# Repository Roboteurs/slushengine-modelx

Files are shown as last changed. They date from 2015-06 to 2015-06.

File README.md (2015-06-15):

# SlushEngine Model:X #

This repository contains the hardware design files for the SlusheEngine. The current design is created on Kicad (BZR 5744). If you wish to contribute to the SlusheEngine project please contact Reiner at info at roboteurs dot com.

If you want to get going on your own project using the SlushEngine please fork it and have fun!

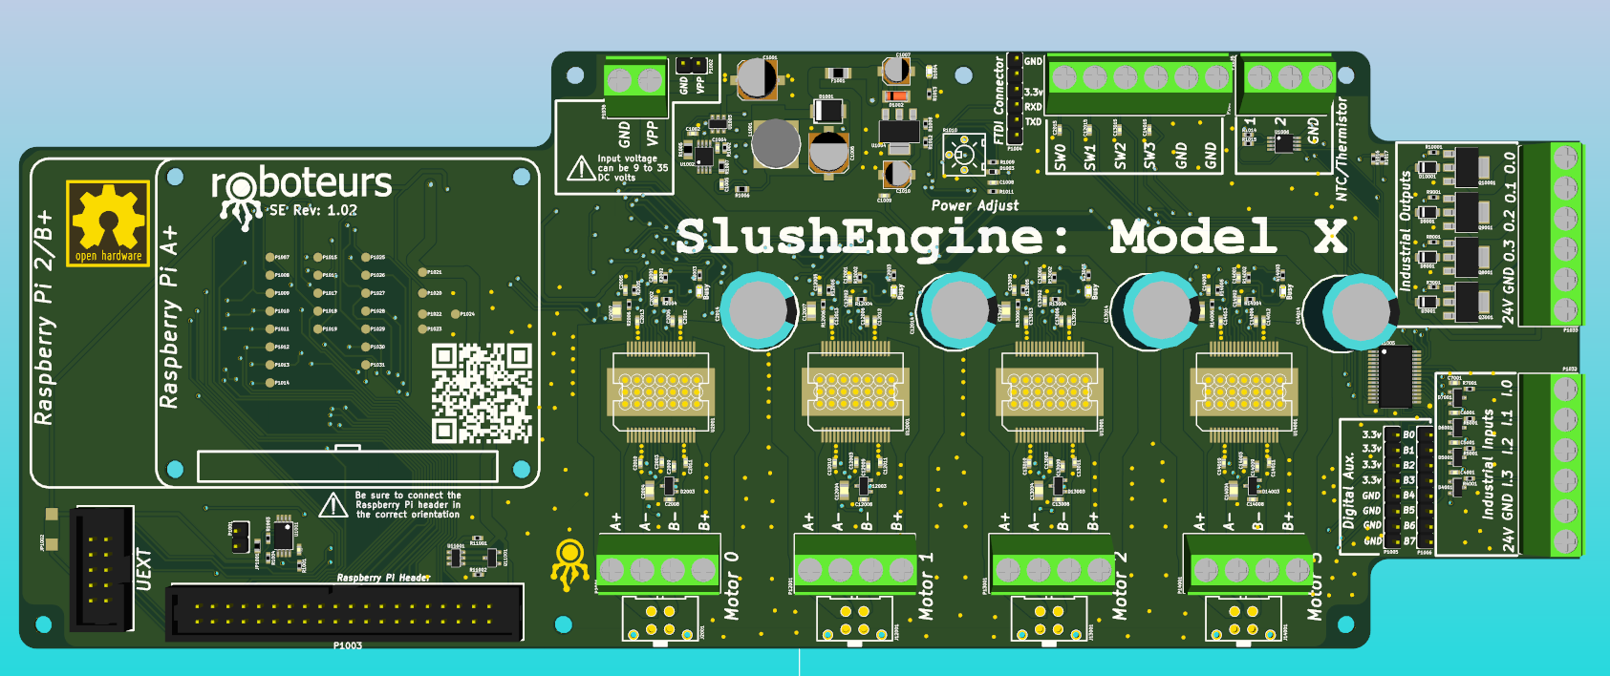
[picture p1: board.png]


## Technical Specifications ##
- Based of L6470 Stepper motor drivers
- Board design to handle 32A on the VPP input
- Supply 5v @ 2A to the Raspberry Pi
- UEXT Connector for expansion modules
- Temperature sensing inputs
- Logic level I/Os and Industrial Level IO (24VDC)
- MAX1164 for temperature sensor handling (2 Channels)
- MCP23017 for I/O expansion on I2C bus
- Raspberry Pi Hat spec eeprom circuit

## Basic Electrical Characteristics ##

- **Max VPP Voltage:** 35VDC
- **Max Current:** 32A
- **No Load Current:** *unkown*
- **Max SPI bus Frequency:** 5Mhz
- **Max Tempratre at L6470L** *unkown*

## Avalible Hardware mods

- **R1010** Can be changed to compensate for off voltage motor (see L6470 datasheet)
- **JP1002** Can be cut to prevent board from powering an expansion module (bottom of the board)

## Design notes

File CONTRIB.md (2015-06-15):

# Contributors and Reference Projects #

We have had a lot of help making the SlushEngine and we want to give credit to all those that helped. Without all of these people, projects and repositories none of this would have been possible.

## Kickstarter Backers ##

Thanks to off you for helping us meet our first production run minimums. Without you SlushEngine would still just be a messy prototype

**Backers Listed in Order of Contribution**
- Dave LeCompte
- Dan Stoneham
- Graham Dixon
- Jerry
- David A. Katz
- James Gonzalez
- Brian Brunswick
- Chris Egloff
- Martin Pike
- Ricardo
- Clive Rixson
- Marcin Kaminski
- SaltyBrains
- Nikolay Kostov
- Davey Rance
- Brian Roy
- Christopher Schneider
- Steve Sutherland
- Pascal M.
- Antony T Curtis
- Drew Harris
- Blufaminol
- John Joseph Mase
- John Vanderlans
- Aaron Price
- George Hope
- Thean Ping
- Jürgen Wittschen
- Ben Hudson
- Tobias Franke
- David B Murray
- Carole Johnston
- Lou O'Block
- John Meyer
- Patrick Dagert
- InSource.Pro
- Mr. Gabor Draskoczy, quickcoating GmbH
- Stan Logan
- MK
- k1ck*thi5
- Chitra
- Tammy Hwang
- Melanie Sodtka
- Alexandru Stan
- Andrew Rossignol
- Shelley McQuade
- Francisco Valera
- David Toma
- Paul Grossman
- Paolo
- GIN
- Charles Burke
- Douglas Petican
- Joon Kim
- Leland Morrison
- Cassandra Dambrosio
- Rikard Westman
- Alice Yeh
- Kelly McDaniel
- Kristen Dyrr
- Axiom Audio
- Julio Terra
- Bogdan Drema

## Project Contributors ##

There are many components to the Slush system and its not easy developing it. But a good team can really help get the Job done, and these poeple where a part of that team.

Alexandru Stan - http://hypertriangle.com/
Andrew Rossignol - http://www.theresistornetwork.com/

## Refrence Projects and Software Tools ##

One of the cool things about the SlushEngine is that it was developed entirely using open source tools! We want to give credit to those tools so that other people can use them as well. There are many diffrent tools that where used and if we missed one please let us know so we can update the list.

- Kicad  http://www.kicad-pcb.org
- Python  https://www.python.org
- Raspberry Pi Foundation - https://www.raspberrypi.org/
- github https://github.com/
- Quick2Wire https://github.com/quick2wire
- SPIDev https://github.com/doceme/py-spidev
- Olimex (UEXT) https://www.olimex.com/

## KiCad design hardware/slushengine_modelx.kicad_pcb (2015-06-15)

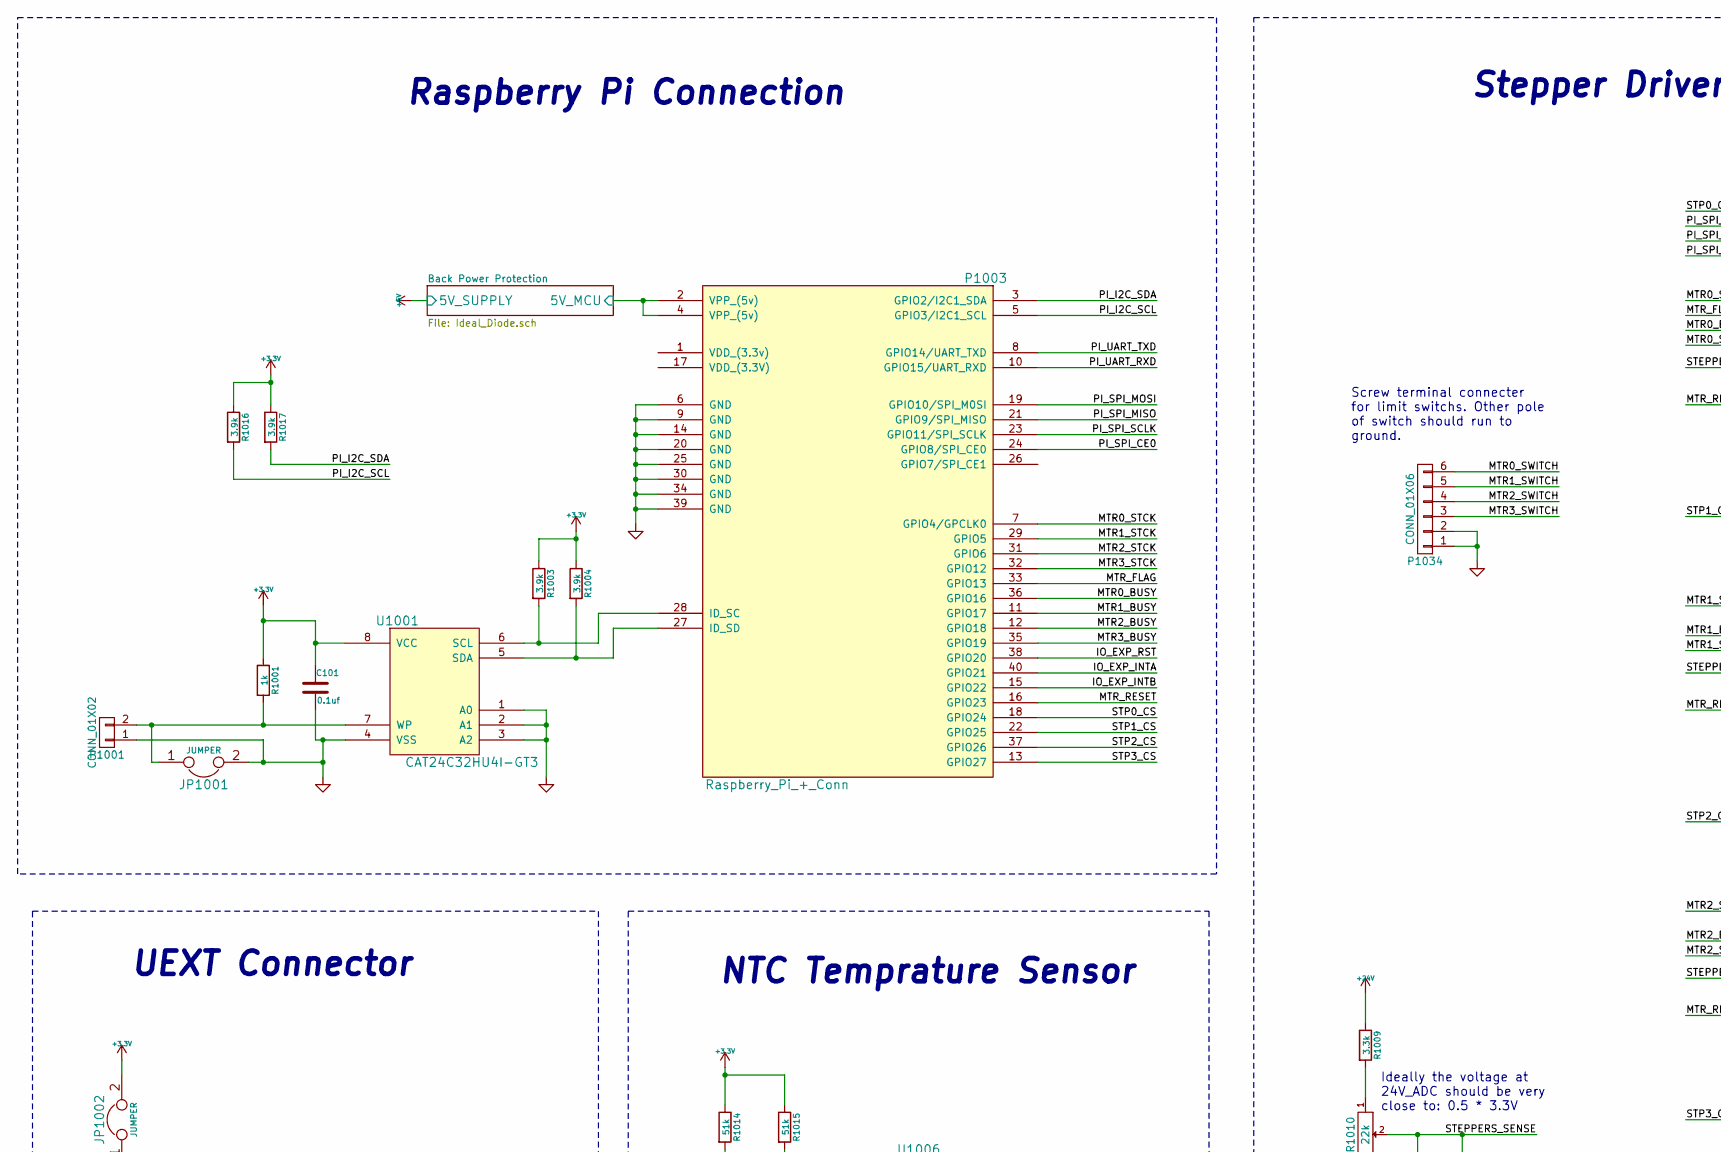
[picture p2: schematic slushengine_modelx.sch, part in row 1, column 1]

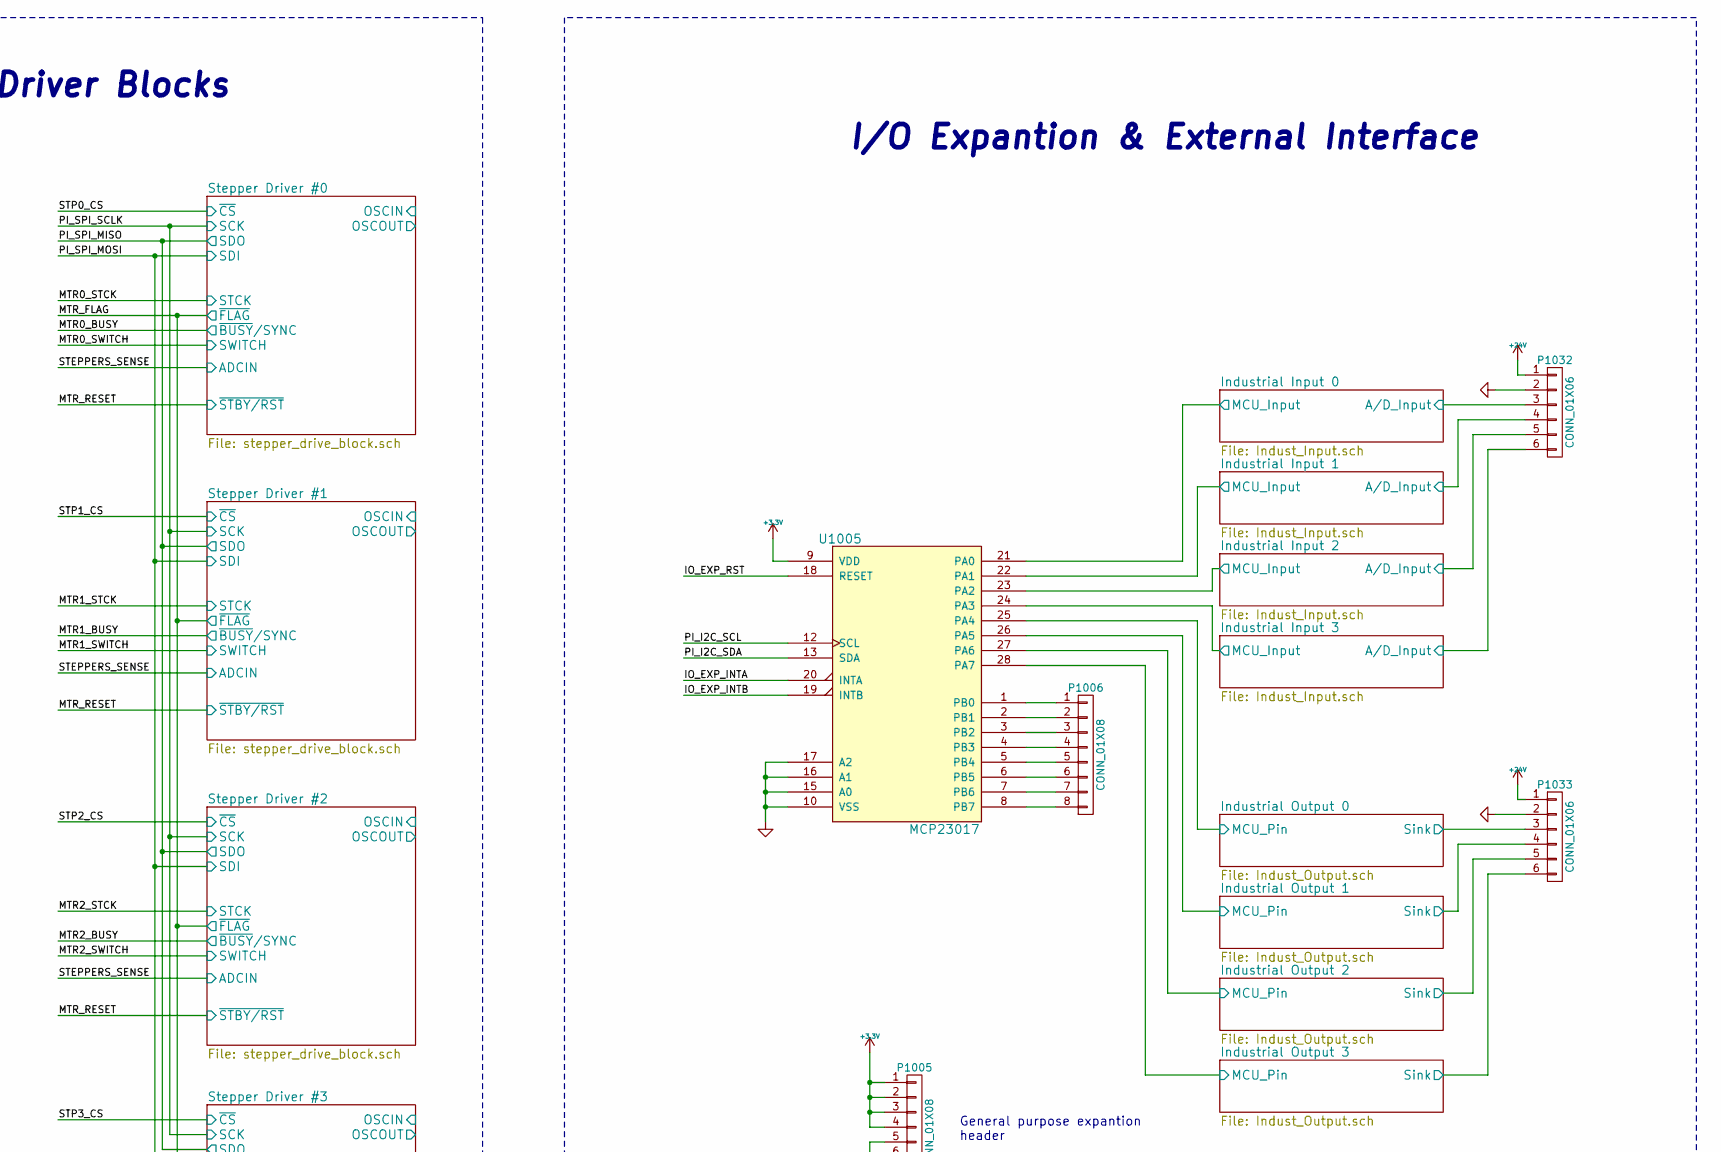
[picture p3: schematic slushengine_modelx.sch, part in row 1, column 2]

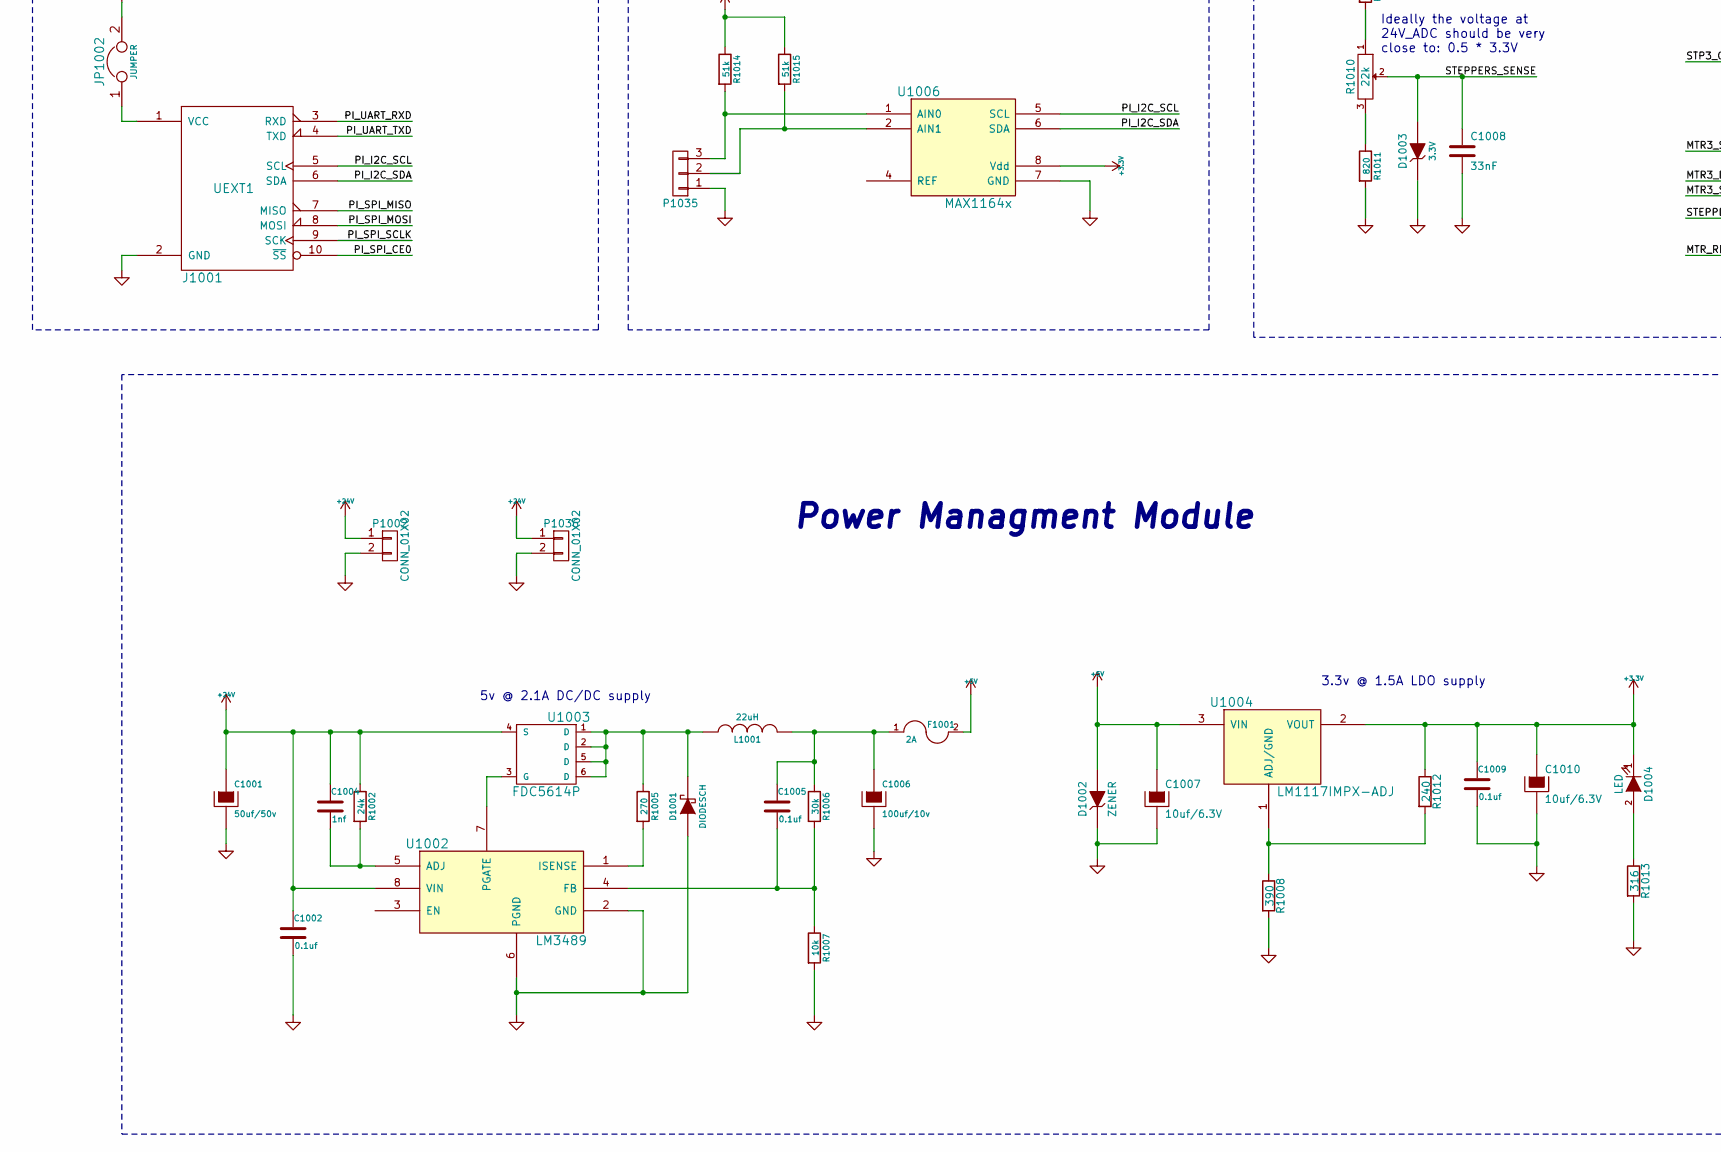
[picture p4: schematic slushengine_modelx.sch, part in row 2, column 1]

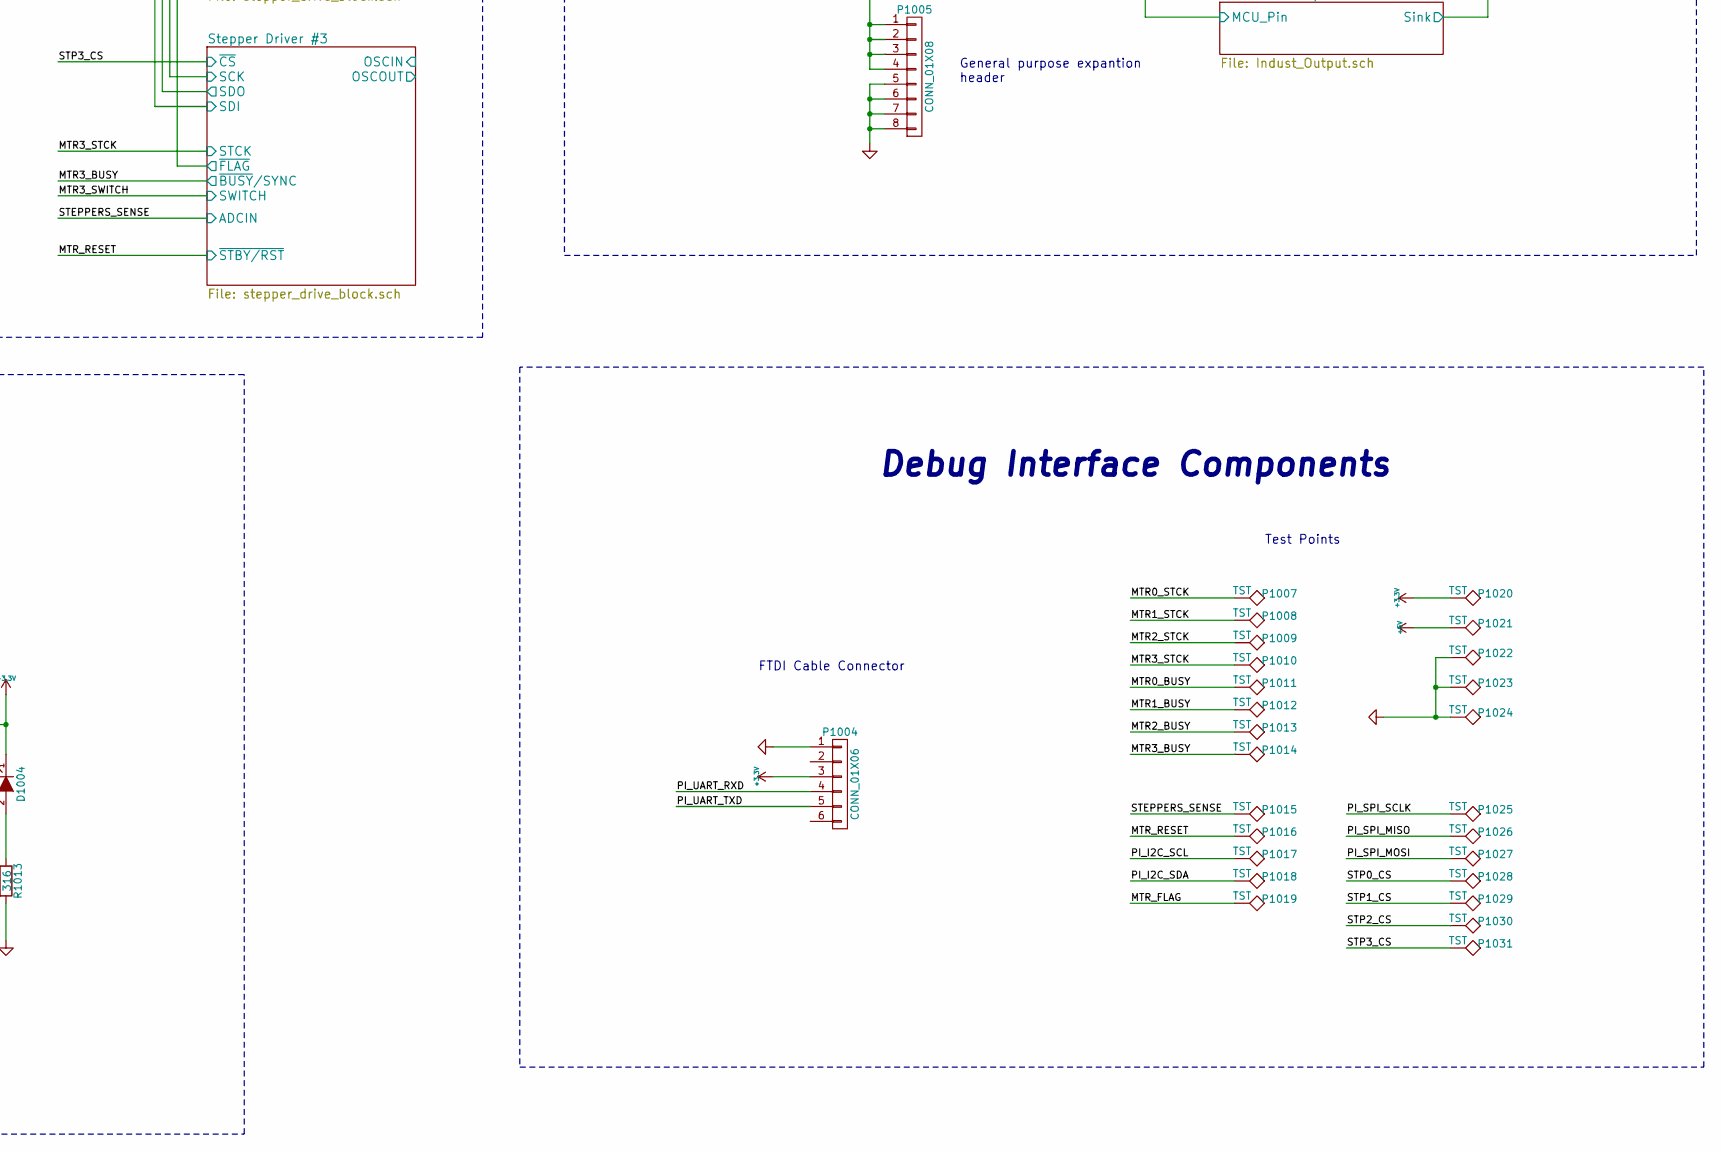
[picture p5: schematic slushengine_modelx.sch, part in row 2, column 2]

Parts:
C101, C1002, C1005, C1009: 0.1uf; c_0402; Mouser Part No. 810-C1005X5R1H104K
C1001: 50uf/50v; c_elec_6.3x7.7; Mouser Part No. 647-UUR1H470MCL6GS
C1004: 1nf; c_0402; Mouser Part No. 810-C1005X5R1H102K
C1006: 100uf/10v; c_elec_6.3x7.7; Mouser Part No. 80-EEV107M016A9GAA
C1007, C1010: 10uf/6.3V; c_elec_4x5.3; Mouser Part No. 80-EEV106M025A9BAA
C1008: 33nF; c_0402; Mouser Part No. 81-GRM36X333K10; Digikey Number 1276-2042-1-ND
D1001: DIODESCH; do214aa; Mouser Part No. 512-MBRS140
D1002: ZENER; sod80c; Mouser Part No. 771-BZV55-C6V2-T/R
D1003: 3.3V; sod523; Mouser Part No. 652-CD0603-Z3V3; Digikey Number CD0603-Z3V3CT-ND
D1004: LED; Led_0603; Mouser Part No. 720-LSQ976-NR-1
F1001: 2A; r_1206; Mouser Part No. 652-MF-NSMF200-2
J1001: UEXT1; vasch_strip_5x2; Mouser Part No. 517-30310-6002; Digikey Number ED1543-ND
JP1001: JUMPER; r_0603
JP1002: JUMPER; NetTie-I_Connected_SMD
L1001: 22uH; inductor_smd_8x5mm; Mouser Part No. 652-SRN8040-220M
P1001: CONN_01X02; pin_strip_2
P1002: CONN_01X02; pin_strip_2; Mouser Part No. 651-1715022
P1003: Raspberry_Pi_+_Conn; vasch_strip_20x2; Mouser Part No. 517-30340-6002
P1004: CONN_01X06; pin_strip_6
P1005, P1006: CONN_01X08; pin_strip_8
P1007, P1008, P1009, P1010, P1011, P1012, P1013, P1014, P1015, P1016, P1017, P1018, P1019, P1020, P1021, P1022, P1023, P1024, P1025, P1026, P1027, P1028, P1029, P1030, P1031: TST; Measurement_Point_Round-SMD-Pad_Small
P1032, P1033, P1034: CONN_01X06; mkds_1,5-6; Mouser Part No. 651-1729160
P1035: CONN_01X03; mkds_1,5-3
P1036: CONN_01X02; mkds_1,5-2
R1001: 1k; r_0402; Mouser Part No. 754-RR0510P-102D
R1002: 24k; r_0402; Mouser Part No. 71-CRCW0402-24K-E3
R1003, R1004, R1016, R1017: 3.9k; r_0402; Mouser Part No. 71-CRCW04023K90FKED
R1005: 270; r_0805; Mouser Part No. 667-ERJ-P06J271V
R1006: 30k; r_0603; Mouser Part No. 594-MCT06030C3002FP5
R1007: 10k; r_0603; Mouser Part No. 71-CRCW0603-10K-E3
R1008: 390; r_0402; Mouser Part No. 594-MCT06030C3900FP5
R1009: 3.3k; r_0402; Mouser Part No. 71-CRCW0402-3.3K-E3; Digikey Number RHM3.3KBGCT-ND
R1010: 22k; 25PR20KLF; Mouser Part No. 858-25PR20KLF
R1011: 820; r_0402; Mouser Part No. 754-RR0510P-821D; Digikey Number 1276-5060-1-ND
R1012: 240; r_0402; Mouser Part No. 754-RR0816P-241D
R1013: 316; r_0402; Mouser Part No. 667-ERJ-2RKF3160X
R1014, R1015: 51k; r_0402; Mouser Part No. 754-RR0510P-513D; Digikey Number 71-CRCW0402-50K-E3
U1001: CAT24C32HU4I-GT3; tssop-8; Mouser Part No. 698-CAT24C32YI-GT3
U1002: LM3489; msoic-8; Mouser Part No. 926-LM3489MM/NOPB
U1003: FDC5614P; sot23-6; Mouser Part No. 512-FDC5614P
U1004: LM1117IMPX-ADJ; sot223; Mouser Part No. 926-M1117IMPXADJNOPB
U1005: MCP23017; ssop-28; Mouser Part No. 579-MCP23017T-E/SS
U1006: MAX1164x; msoic-8; Mouser Part No. 700-MAX11647EUA

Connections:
+3V3: C101.1, C1009.1, C1010.1, D1004.1 (K), JP1002.2, P1004.3, P1005.1, P1005.2, P1005.3, P1005.4, P1020.1, R1001.1, R1003.1, R1004.1, R1012.1, R1014.1, R1015.1, R1016.1, R1017.1, U1001.8 (VCC), U1004.2 (VOUT), U1005.9 (VDD), U1006.8 (Vdd); also elsewhere on the board
+5V: C1007.1, D1002.2 (A), F1001.2, P1021.1, U1004.3 (VIN); also elsewhere on the board
+24V: C1001.1, C1002.1, C1004.1, P1002.1, P1032.1, P1033.1, P1036.1, R1002.1, R1009.1, U1002.8 (VIN), U1003.4 (S); also elsewhere on the board
/Back Power Protection/5V_MCU: P1003.2 (VPP_(5v)), P1003.4 (VPP_(5v)); also elsewhere on the board
/IO_EXP_INTA: P1003.40 (GPIO21), U1005.20 (INTA)
/IO_EXP_INTB: P1003.15 (GPIO22), U1005.19 (INTB)
/IO_EXP_RST: P1003.38 (GPIO20), U1005.18 (RESET)
/Industrial Input 0/A/D_Input: P1032.3; also elsewhere on the board
/Industrial Input 0/MCU_Input: U1005.21 (PA0); also elsewhere on the board
/Industrial Input 1/A/D_Input: P1032.4; also elsewhere on the board
/Industrial Input 1/MCU_Input: U1005.22 (PA1); also elsewhere on the board
/Industrial Input 2/A/D_Input: P1032.5; also elsewhere on the board
/Industrial Input 2/MCU_Input: U1005.23 (PA2); also elsewhere on the board
/Industrial Input 3/A/D_Input: P1032.6; also elsewhere on the board
/Industrial Input 3/MCU_Input: U1005.24 (PA3); also elsewhere on the board
/Industrial Output 0/MCU_Pin: U1005.25 (PA4); also elsewhere on the board
/Industrial Output 0/Sink: P1033.3; also elsewhere on the board
/Industrial Output 1/MCU_Pin: U1005.26 (PA5); also elsewhere on the board
/Industrial Output 1/Sink: P1033.4; also elsewhere on the board
/Industrial Output 2/MCU_Pin: U1005.27 (PA6); also elsewhere on the board
/Industrial Output 2/Sink: P1033.5; also elsewhere on the board
/Industrial Output 3/MCU_Pin: U1005.28 (PA7); also elsewhere on the board
/Industrial Output 3/Sink: P1033.6; also elsewhere on the board
/PI_I2C_SCL: J1001.5 (SCL), P1003.5 (GPIO3/I2C1_SCL), P1017.1, R1016.2, U1005.12 (SCL), U1006.5 (SCL)
/PI_I2C_SDA: J1001.6 (SDA), P1003.3 (GPIO2/I2C1_SDA), P1018.1, R1017.2, U1005.13 (SDA), U1006.6 (SDA)
/PI_SPI_CE0: J1001.10 (~SS), P1003.24 (GPIO8/SPI_CE0)
/PI_UART_RXD: J1001.3 (RXD), P1003.10 (GPIO15/UART_RXD), P1004.4
/PI_UART_TXD: J1001.4 (TXD), P1003.8 (GPIO14/UART_TXD), P1004.5
/Stepper Driver #0/ADCIN: C1008.1, D1003.2 (A), P1015.1, R1010.2; also elsewhere on the board
/Stepper Driver #0/SCK: J1001.9 (SCK), P1003.23 (GPIO11/SPI_SCLK), P1025.1; also elsewhere on the board
/Stepper Driver #0/SDI: J1001.8 (MOSI), P1003.19 (GPIO10/SPI_M0SI), P1027.1; also elsewhere on the board
/Stepper Driver #0/SDO: J1001.7 (MISO), P1003.21 (GPIO9/SPI_MISO), P1026.1; also elsewhere on the board
/Stepper Driver #0/STCK: P1003.7 (GPIO4/GPCLK0), P1007.1; also elsewhere on the board
/Stepper Driver #0/~BUSY~/SYNC: P1003.36 (GPIO16), P1011.1; also elsewhere on the board
/Stepper Driver #0/~CS: P1003.18 (GPIO24), P1028.1; also elsewhere on the board
/Stepper Driver #0/~FLAG: P1003.33 (GPIO13), P1019.1; also elsewhere on the board
/Stepper Driver #0/~STBY/RST: P1003.16 (GPIO23), P1016.1; also elsewhere on the board
/Stepper Driver #1/STCK: P1003.29 (GPIO5), P1008.1; also elsewhere on the board
/Stepper Driver #1/~BUSY~/SYNC: P1003.11 (GPIO17), P1012.1; also elsewhere on the board
/Stepper Driver #1/~CS: P1003.22 (GPIO25), P1029.1; also elsewhere on the board
/Stepper Driver #2/STCK: P1003.31 (GPIO6), P1009.1; also elsewhere on the board
/Stepper Driver #2/SWITCH: P1034.4; also elsewhere on the board
/Stepper Driver #2/~BUSY~/SYNC: P1003.12 (GPIO18), P1013.1; also elsewhere on the board
/Stepper Driver #2/~CS: P1003.37 (GPIO26), P1030.1; also elsewhere on the board
/Stepper Driver #3/STCK: P1003.32 (GPIO12), P1010.1; also elsewhere on the board
/Stepper Driver #3/SWITCH: P1034.3; also elsewhere on the board
/Stepper Driver #3/~BUSY~/SYNC: P1003.35 (GPIO19), P1014.1; also elsewhere on the board
/Stepper Driver #3/~CS: P1003.13 (GPIO27), P1031.1; also elsewhere on the board
GND: C101.2, C1001.2, C1002.2, C1006.2, C1007.2, C1008.2, C1009.2, C1010.2, D1001.1 (A), D1002.1 (K), D1003.1 (K), J1001.2 (GND), JP1001.2, P1001.1, P1002.2, P1003.6 (GND), P1003.9 (GND), P1003.14 (GND), P1003.20 (GND), P1003.25 (GND), P1003.30 (GND), P1003.34 (GND), P1003.39 (GND), P1004.1, P1005.5, P1005.6, P1005.7, P1005.8, P1022.1, P1023.1, P1024.1, P1032.2, P1033.2, P1034.1, P1034.2, P1035.1, P1036.2, R1007.2, R1008.2, R1011.2, R1013.2, U1001.1 (A0), U1001.2 (A1), U1001.3 (A2), U1001.4 (VSS), U1002.2 (GND), U1002.6 (PGND), U1005.10 (VSS), U1005.15 (A0), U1005.16 (A1), U1005.17 (A2), U1006.7 (GND); also elsewhere on the board
unnamed: C1004.2, R1002.2, U1002.5 (ADJ)
unnamed: C1005.1, C1006.1, F1001.1, L1001.2, R1006.1
unnamed: C1005.2, R1006.2, R1007.1, U1002.4 (FB)
unnamed: D1001.2 (K), L1001.1, R1005.1, U1003.1 (D), U1003.2 (D), U1003.5 (D), U1003.6 (D)
unnamed: D1004.2 (A), R1013.1
unnamed: J1001.1 (VCC), JP1002.1
unnamed: JP1001.1, P1001.2, R1001.2, U1001.7 (WP)
unnamed: P1003.27 (ID_SD), R1004.2, U1001.5 (SDA)
unnamed: P1003.28 (ID_SC), R1003.2, U1001.6 (SCL)
unnamed: P1006.1, U1005.1 (PB0)
unnamed: P1006.2, U1005.2 (PB1)
unnamed: P1006.3, U1005.3 (PB2)
unnamed: P1006.4, U1005.4 (PB3)
unnamed: P1006.5, U1005.5 (PB4)
unnamed: P1006.6, U1005.6 (PB5)
unnamed: P1006.7, U1005.7 (PB6)
unnamed: P1006.8, U1005.8 (PB7)
unnamed: P1035.2, R1015.2, U1006.2 (AIN1)
unnamed: P1035.3, R1014.2, U1006.1 (AIN0)
unnamed: R1005.2, U1002.1 (ISENSE)
unnamed: R1008.1, R1012.2, U1004.1 (ADJ/GND)
unnamed: R1009.2, R1010.1
unnamed: R1010.3, R1011.1
unnamed: U1002.7 (PGATE), U1003.3 (G)

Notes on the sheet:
Ideally the voltage at 24V_ADC should be very close to: 0.5 * 3.3V
Raspberry Pi Connection
Stepper Driver Blocks
I/O Expantion & External Interface
Power Managment Module
General purpose expantion header
5v @ 2.1A DC/DC supply
3.3v @ 1.5A LDO supply
Debug Interface Components
Test Points
FTDI Cable Connector
UEXT Connector
Screw terminal connecter for limit switchs. Other pole of switch should run to ground.
NTC Temprature Sensor

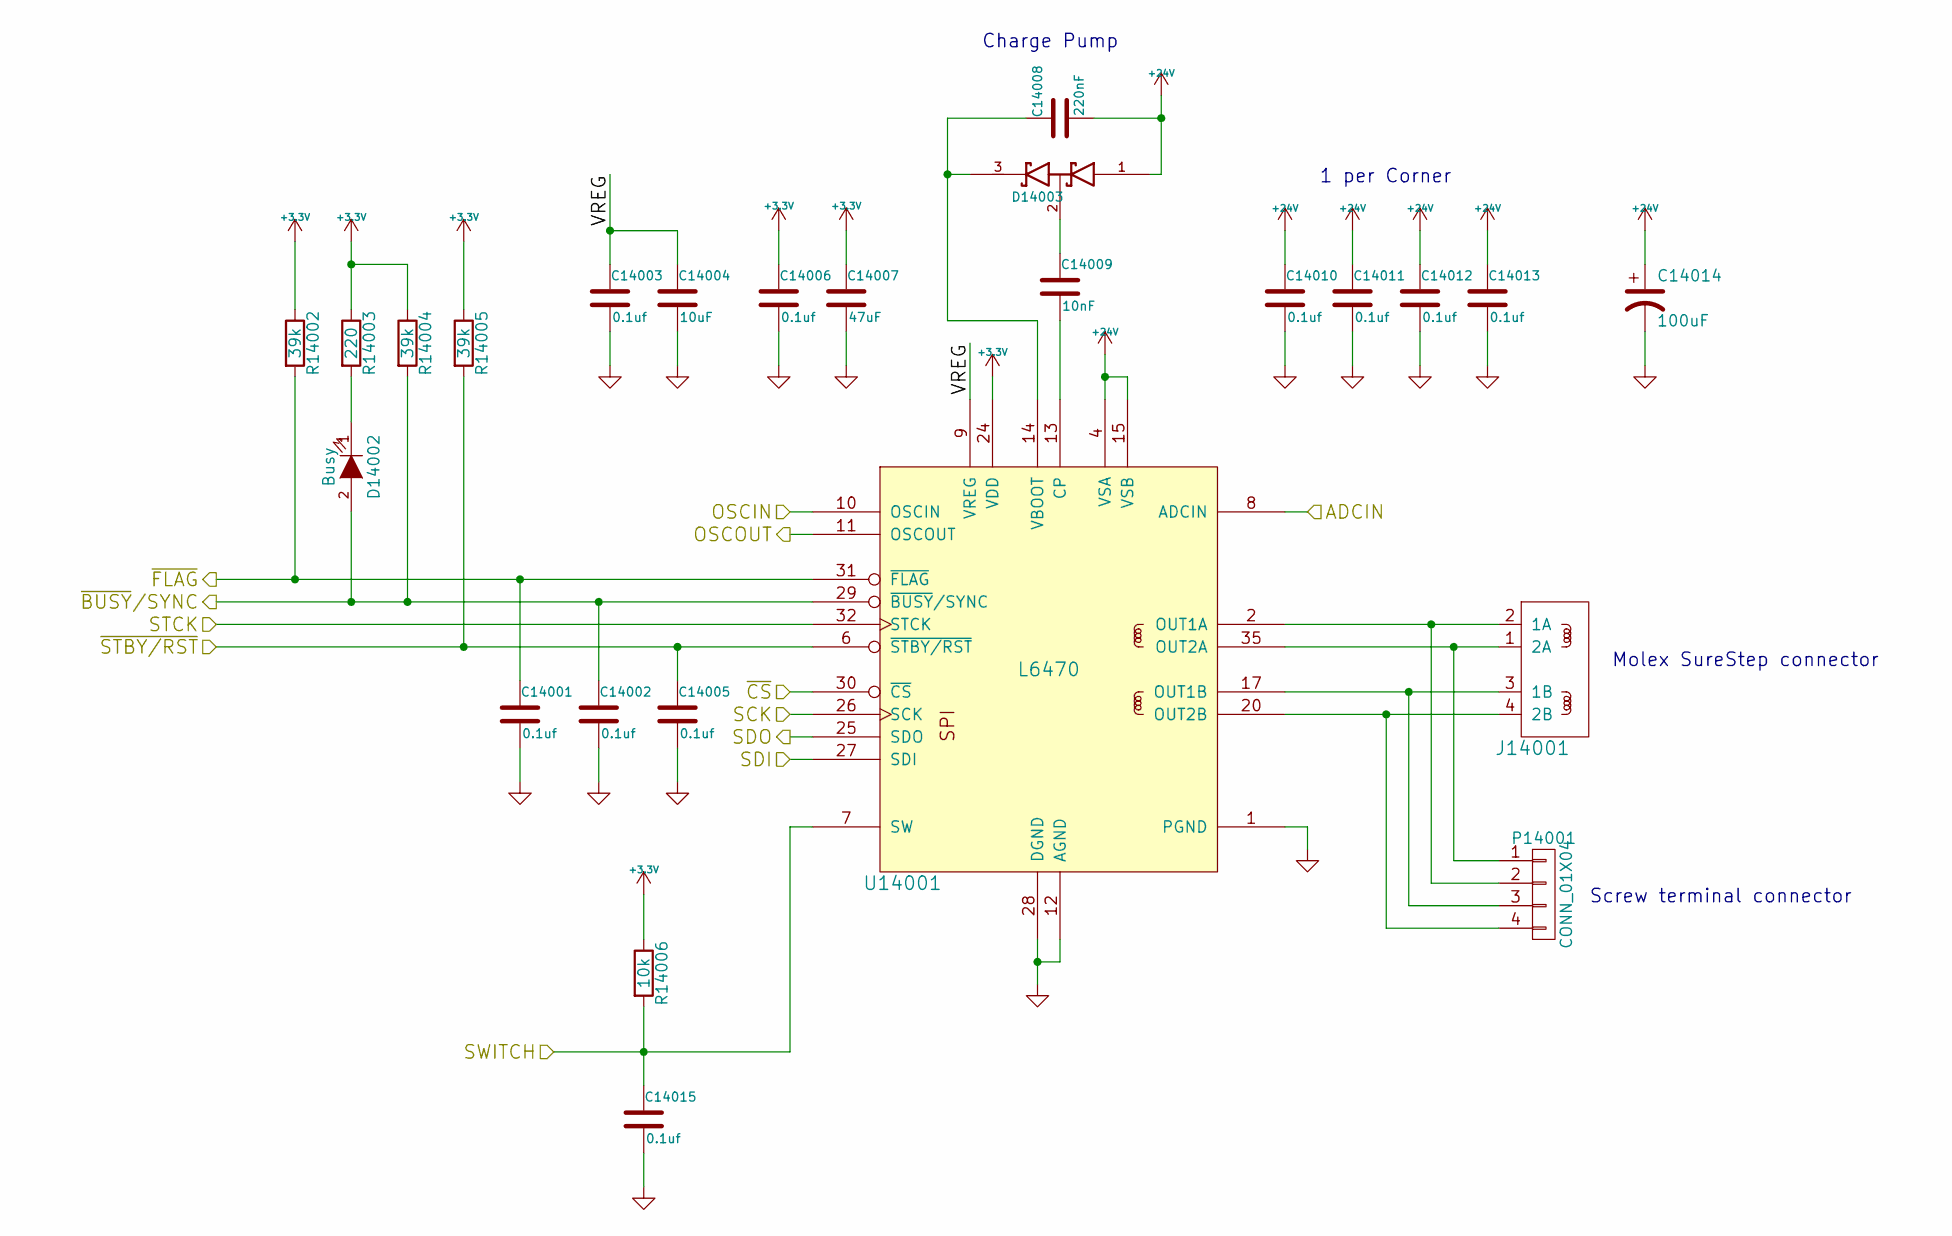
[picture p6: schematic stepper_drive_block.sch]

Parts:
C2001, C2002, C2003, C2005, C2006, C2010, C2011, C2012, C2013, C12015: 0.1uf; c_0402; Mouser Part No. 810-C1005X5R1H104K; Digikey Number 1276-2163-1-ND
C2004: 10uF; c_0805; Mouser Part No. 81-GRM219R61E106KA2D; Digikey Number 1276-1119-1-ND
C2007: 47uF; c_0805; Mouser Part No. 963-JMK212BJ476MG-T; Digikey Number 1276-2420-1-ND
C2008: 220nF; c_0402; Mouser Part No. 810-CGA2B1X7R1V224KC; Digikey Number 1276-2949-1-ND
C2009: 10nF; c_0402; Mouser Part No. 81-GRM155R71H103KA8D; Digikey Number 445-1304-1-ND
C2014: 100uF; CP_12.5x25mm; Mouser Part No. 667-EEU-EE2C101; Digikey Number P13622-ND
D2002: Busy; Led_0603; Mouser Part No. 696-SML-LX0603SUGW; Digikey Number 67-1693-1-ND
D2003: DOUBLE_SCHOTTKY; sot23; Mouser Part No. 833-BAS70-04-TP; Digikey Number BAS70-04TPMSCT-ND
J2001: Stepper Motor; SureStep_CONN; Mouser Part No. 538-43045-0412; Digikey Number 281-1437-ND
P2001: CONN_01X04; mkds_1,5-4; Mouser Part No. 651-1729144
R2002, R2004, R2005: 39k; r_0402; Mouser Part No. 754-RR0510P-393D; Digikey Number 1276-5100-1-ND
R2003: 220; r_0402; Mouser Part No. 667-ERA-2AED221X; Digikey Number 1276-5046-1-ND
R2006: 10k; r_0402; Mouser Part No. 754-RR0510P-103D; Digikey Number 1276-5086-1-ND
U2001: L6470; POWERSO-36; Mouser Part No. 511-L6470PD

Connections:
+3V3: C2006.1, C2007.1, R2002.1, R2003.1, R2004.1, R2005.1, R2006.1, U2001.24 (VDD); also elsewhere on the board
+24V: C2008.2, C2010.1, C2011.1, C2012.1, C2013.1, C2014.1, D2003.1 (Anode), U2001.4 (VSA), U2001.5 (VSA), U2001.15 (VSB), U2001.16 (VSB), U2001.22 (VSB), U2001.23 (VSB), U2001.33 (VSA), U2001.34 (VSA); also elsewhere on the board
/Stepper Driver #0/ADCIN: U2001.8 (ADCIN); also elsewhere on the board
/Stepper Driver #0/OSCIN: U2001.10 (OSCIN)
/Stepper Driver #0/OSCOUT: U2001.11 (OSCOUT)
/Stepper Driver #0/SCK: U2001.26 (SCK); also elsewhere on the board
/Stepper Driver #0/SDI: U2001.27 (SDI); also elsewhere on the board
/Stepper Driver #0/SDO: U2001.25 (SDO); also elsewhere on the board
/Stepper Driver #0/STCK: U2001.32 (STCK); also elsewhere on the board
/Stepper Driver #0/VREG: C2003.1, C2004.1, U2001.9 (VREG)
/Stepper Driver #0/~BUSY~/SYNC: C2002.1, D2002.2 (A), R2004.2, U2001.29 (~BUSY~/SYNC); also elsewhere on the board
/Stepper Driver #0/~CS: U2001.30 (~CS); also elsewhere on the board
/Stepper Driver #0/~FLAG: C2001.1, R2002.2, U2001.31 (~FLAG); also elsewhere on the board
/Stepper Driver #0/~STBY/RST: C2005.1, R2005.2, U2001.6 (~STBY/RST); also elsewhere on the board
GND: C2001.2, C2002.2, C2003.2, C2004.2, C2005.2, C2006.2, C2007.2, C2010.2, C2011.2, C2012.2, C2013.2, C2014.2, C12015.2, U2001.1 (PGND), U2001.12 (AGND), U2001.19 (PGND), U2001.28 (DGND), U2001.PAD (PGND); also elsewhere on the board
unnamed: C2008.1, D2003.3 (cathode), U2001.14 (VBOOT)
unnamed: C2009.1, D2003.2 (AK)
unnamed: C2009.2, U2001.13 (CP)
unnamed: D2002.1 (K), R2003.2
unnamed: J2001.1 (2A), P2001.1, U2001.35 (OUT2A), U2001.36 (OUT2A)
unnamed: J2001.2 (1A), P2001.2, U2001.2 (OUT1A), U2001.3 (OUT1A)
unnamed: J2001.3 (1B), P2001.3, U2001.17 (OUT1B), U2001.18 (OUT1B)
unnamed: J2001.4 (2B), P2001.4, U2001.20 (OUT2B), U2001.21 (OUT2B)

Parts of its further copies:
C2015, C12001, C12002, C12003, C12005, C12006, C12010, C12011, C12012, C12013, C13001, C13002, C13003, C13005, C13006, C13010, C13011, C13012, C13013, C13015, C14001, C14002, C14003, C14005, C14006, C14010, C14011, C14012, C14013, C14015: 0.1uf; c_0402; Mouser Part No. 810-C1005X5R1H104K; Digikey Number 1276-2163-1-ND
C12004, C13004, C14004: 10uF; c_0805; Mouser Part No. 81-GRM219R61E106KA2D; Digikey Number 1276-1119-1-ND
C12007, C13007, C14007: 47uF; c_0805; Mouser Part No. 963-JMK212BJ476MG-T; Digikey Number 1276-2420-1-ND
C12008, C13008, C14008: 220nF; c_0402; Mouser Part No. 810-CGA2B1X7R1V224KC; Digikey Number 1276-2949-1-ND
C12009, C13009, C14009: 10nF; c_0402; Mouser Part No. 81-GRM155R71H103KA8D; Digikey Number 445-1304-1-ND
C12014, C13014, C14014: 100uF; CP_12.5x25mm; Mouser Part No. 667-EEU-EE2C101; Digikey Number P13622-ND
D12002, D13002, D14002: Busy; Led_0603; Mouser Part No. 696-SML-LX0603SUGW; Digikey Number 67-1693-1-ND
D12003, D13003, D14003: DOUBLE_SCHOTTKY; sot23; Mouser Part No. 833-BAS70-04-TP; Digikey Number BAS70-04TPMSCT-ND
J12001, J13001, J14001: Stepper Motor; SureStep_CONN; Mouser Part No. 538-43045-0412; Digikey Number 281-1437-ND
P12001, P13001, P14001: CONN_01X04; mkds_1,5-4; Mouser Part No. 651-1729144
R12002, R12004, R12005, R13002, R13004, R13005, R14002, R14004, R14005: 39k; r_0402; Mouser Part No. 754-RR0510P-393D; Digikey Number 1276-5100-1-ND
R12003, R13003, R14003: 220; r_0402; Mouser Part No. 667-ERA-2AED221X; Digikey Number 1276-5046-1-ND
R12006, R13006, R14006: 10k; r_0402; Mouser Part No. 754-RR0510P-103D; Digikey Number 1276-5086-1-ND
U12001, U13001, U14001: L6470; POWERSO-36; Mouser Part No. 511-L6470PD

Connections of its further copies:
+3V3: C12006.1, C12007.1, C13006.1, C13007.1, C14006.1, C14007.1, R12002.1, R12003.1, R12004.1, R12005.1, R12006.1, R13002.1, R13003.1, R13004.1, R13005.1, R13006.1, R14002.1, R14003.1, R14004.1, R14005.1, R14006.1, U12001.24 (VDD), U13001.24 (VDD), U14001.24 (VDD); also elsewhere on the board
+24V: C12008.2, C12010.1, C12011.1, C12012.1, C12013.1, C12014.1, C13008.2, C13010.1, C13011.1, C13012.1, C13013.1, C13014.1, C14008.2, C14010.1, C14011.1, C14012.1, C14013.1, C14014.1, D12003.1 (Anode), D13003.1 (Anode), D14003.1 (Anode), U12001.4 (VSA), U12001.5 (VSA), U12001.15 (VSB), U12001.16 (VSB), U12001.22 (VSB), U12001.23 (VSB), U12001.33 (VSA), U12001.34 (VSA), U13001.4 (VSA), U13001.5 (VSA), U13001.15 (VSB), U13001.16 (VSB), U13001.22 (VSB), U13001.23 (VSB), U13001.33 (VSA), U13001.34 (VSA), U14001.4 (VSA), U14001.5 (VSA), U14001.15 (VSB), U14001.16 (VSB), U14001.22 (VSB), U14001.23 (VSB), U14001.33 (VSA), U14001.34 (VSA); also elsewhere on the board
/Stepper Driver #0/ADCIN: U12001.8 (ADCIN), U13001.8 (ADCIN), U14001.8 (ADCIN); also elsewhere on the board
/Stepper Driver #0/SCK: U12001.26 (SCK), U13001.26 (SCK), U14001.26 (SCK); also elsewhere on the board
/Stepper Driver #0/SDI: U12001.27 (SDI), U13001.27 (SDI), U14001.27 (SDI); also elsewhere on the board
/Stepper Driver #0/SDO: U12001.25 (SDO), U13001.25 (SDO), U14001.25 (SDO); also elsewhere on the board
/Stepper Driver #0/~FLAG: C12001.1, C13001.1, C14001.1, R12002.2, R13002.2, R14002.2, U12001.31 (~FLAG), U13001.31 (~FLAG), U14001.31 (~FLAG); also elsewhere on the board
/Stepper Driver #0/~STBY/RST: C12005.1, C13005.1, C14005.1, R12005.2, R13005.2, R14005.2, U12001.6 (~STBY/RST), U13001.6 (~STBY/RST), U14001.6 (~STBY/RST); also elsewhere on the board
/Stepper Driver #1/OSCIN: U12001.10 (OSCIN)
/Stepper Driver #1/OSCOUT: U12001.11 (OSCOUT)
/Stepper Driver #1/STCK: U12001.32 (STCK); also elsewhere on the board
/Stepper Driver #1/VREG: C12003.1, C12004.1, U12001.9 (VREG)
/Stepper Driver #1/~BUSY~/SYNC: C12002.1, D12002.2 (A), R12004.2, U12001.29 (~BUSY~/SYNC); also elsewhere on the board
/Stepper Driver #1/~CS: U12001.30 (~CS); also elsewhere on the board
/Stepper Driver #2/OSCIN: U13001.10 (OSCIN)
/Stepper Driver #2/OSCOUT: U13001.11 (OSCOUT)
/Stepper Driver #2/STCK: U13001.32 (STCK); also elsewhere on the board
/Stepper Driver #2/SWITCH: C13015.1, R13006.2, U13001.7 (SW); also elsewhere on the board
/Stepper Driver #2/VREG: C13003.1, C13004.1, U13001.9 (VREG)
/Stepper Driver #2/~BUSY~/SYNC: C13002.1, D13002.2 (A), R13004.2, U13001.29 (~BUSY~/SYNC); also elsewhere on the board
/Stepper Driver #2/~CS: U13001.30 (~CS); also elsewhere on the board
/Stepper Driver #3/OSCIN: U14001.10 (OSCIN)
/Stepper Driver #3/OSCOUT: U14001.11 (OSCOUT)
/Stepper Driver #3/STCK: U14001.32 (STCK); also elsewhere on the board
/Stepper Driver #3/SWITCH: C14015.1, R14006.2, U14001.7 (SW); also elsewhere on the board
/Stepper Driver #3/VREG: C14003.1, C14004.1, U14001.9 (VREG)
/Stepper Driver #3/~BUSY~/SYNC: C14002.1, D14002.2 (A), R14004.2, U14001.29 (~BUSY~/SYNC); also elsewhere on the board
/Stepper Driver #3/~CS: U14001.30 (~CS); also elsewhere on the board
GND: C2015.2, C12001.2, C12002.2, C12003.2, C12004.2, C12005.2, C12006.2, C12007.2, C12010.2, C12011.2, C12012.2, C12013.2, C12014.2, C13001.2, C13002.2, C13003.2, C13004.2, C13005.2, C13006.2, C13007.2, C13010.2, C13011.2, C13012.2, C13013.2, C13014.2, C13015.2, C14001.2, C14002.2, C14003.2, C14004.2, C14005.2, C14006.2, C14007.2, C14010.2, C14011.2, C14012.2, C14013.2, C14014.2, C14015.2, U12001.1 (PGND), U12001.12 (AGND), U12001.19 (PGND), U12001.28 (DGND), U12001.PAD (PGND), U13001.1 (PGND), U13001.12 (AGND), U13001.19 (PGND), U13001.28 (DGND), U13001.PAD (PGND), U14001.1 (PGND), U14001.12 (AGND), U14001.19 (PGND), U14001.28 (DGND), U14001.PAD (PGND); also elsewhere on the board
unnamed: C12008.1, D12003.3 (cathode), U12001.14 (VBOOT)
unnamed: C12009.1, D12003.2 (AK)
unnamed: C12009.2, U12001.13 (CP)
unnamed: C13008.1, D13003.3 (cathode), U13001.14 (VBOOT)
unnamed: C13009.1, D13003.2 (AK)
unnamed: C13009.2, U13001.13 (CP)
unnamed: C14008.1, D14003.3 (cathode), U14001.14 (VBOOT)
unnamed: C14009.1, D14003.2 (AK)
unnamed: C14009.2, U14001.13 (CP)
unnamed: D12002.1 (K), R12003.2
unnamed: D13002.1 (K), R13003.2
unnamed: D14002.1 (K), R14003.2
unnamed: J12001.1 (2A), P12001.1, U12001.35 (OUT2A), U12001.36 (OUT2A)
unnamed: J12001.2 (1A), P12001.2, U12001.2 (OUT1A), U12001.3 (OUT1A)
unnamed: J12001.3 (1B), P12001.3, U12001.17 (OUT1B), U12001.18 (OUT1B)
unnamed: J12001.4 (2B), P12001.4, U12001.20 (OUT2B), U12001.21 (OUT2B)
unnamed: J13001.1 (2A), P13001.1, U13001.35 (OUT2A), U13001.36 (OUT2A)
unnamed: J13001.2 (1A), P13001.2, U13001.2 (OUT1A), U13001.3 (OUT1A)
unnamed: J13001.3 (1B), P13001.3, U13001.17 (OUT1B), U13001.18 (OUT1B)
unnamed: J13001.4 (2B), P13001.4, U13001.20 (OUT2B), U13001.21 (OUT2B)
unnamed: J14001.1 (2A), P14001.1, U14001.35 (OUT2A), U14001.36 (OUT2A)
unnamed: J14001.2 (1A), P14001.2, U14001.2 (OUT1A), U14001.3 (OUT1A)
unnamed: J14001.3 (1B), P14001.3, U14001.17 (OUT1B), U14001.18 (OUT1B)
unnamed: J14001.4 (2B), P14001.4, U14001.20 (OUT2B), U14001.21 (OUT2B)

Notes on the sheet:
1 per Corner
Charge Pump
Molex SureStep connector
Screw terminal connector

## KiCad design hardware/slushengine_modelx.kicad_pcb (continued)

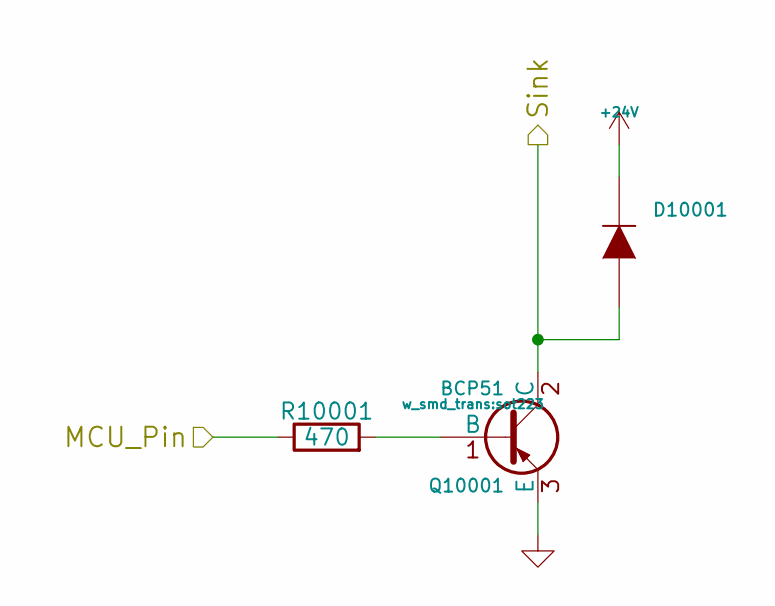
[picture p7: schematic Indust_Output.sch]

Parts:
D3001: RSX501L-20TE25; do219ab; Mouser Part No. 78-S07J; Digikey Number RSX501L-20TE25CT-ND
Q3001: BCP51; sot223; Mouser Part No. 863-NJT4031NT1G
R3001: 470; r_0402; Mouser Part No. 71-CRCW0402-470-E3; Digikey Number 1276-5054-1-ND

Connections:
+24V: D3001.2 (K); also elsewhere on the board
/Industrial Output 0/MCU_Pin: R3001.1; also elsewhere on the board
/Industrial Output 0/Sink: D3001.1 (A), Q3001.2 (C); also elsewhere on the board
GND: Q3001.3 (E); also elsewhere on the board
unnamed: Q3001.1 (B), R3001.2

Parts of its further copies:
D8001, D9001, D10001: RSX501L-20TE25; do219ab; Mouser Part No. 78-S07J; Digikey Number RSX501L-20TE25CT-ND
Q8001, Q9001, Q10001: BCP51; sot223; Mouser Part No. 863-NJT4031NT1G
R8001, R9001, R10001: 470; r_0402; Mouser Part No. 71-CRCW0402-470-E3; Digikey Number 1276-5054-1-ND

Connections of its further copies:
+24V: D8001.2 (K), D9001.2 (K), D10001.2 (K); also elsewhere on the board
/Industrial Output 1/MCU_Pin: R8001.1; also elsewhere on the board
/Industrial Output 1/Sink: D8001.1 (A), Q8001.2 (C); also elsewhere on the board
/Industrial Output 2/MCU_Pin: R9001.1; also elsewhere on the board
/Industrial Output 2/Sink: D9001.1 (A), Q9001.2 (C); also elsewhere on the board
/Industrial Output 3/MCU_Pin: R10001.1; also elsewhere on the board
/Industrial Output 3/Sink: D10001.1 (A), Q10001.2 (C); also elsewhere on the board
GND: Q8001.3 (E), Q9001.3 (E), Q10001.3 (E); also elsewhere on the board
unnamed: Q8001.1 (B), R8001.2
unnamed: Q9001.1 (B), R9001.2
unnamed: Q10001.1 (B), R10001.2

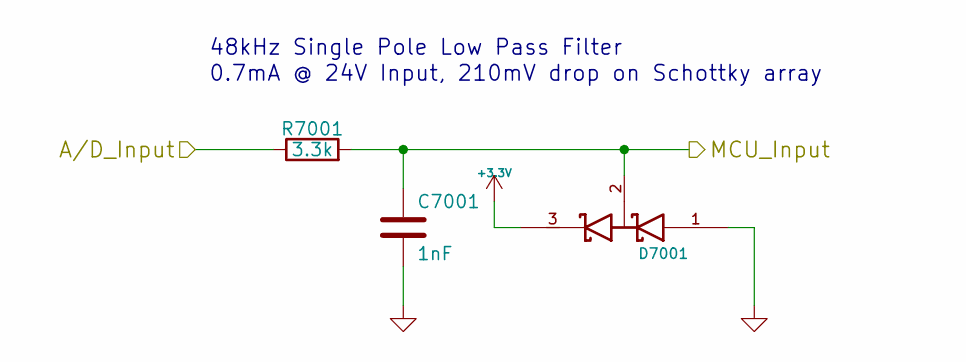
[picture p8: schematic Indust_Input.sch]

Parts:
C4001: 1nF; c_0402; Mouser Part No. 810-C1005C0G2A102J5C; Digikey Number 1276-1913-1-ND
D4001: 1SS295; sot23; Mouser Part No. 757-1SS295TE85LF; Digikey Number 1SS295(TE85LF)CT-ND
R4001: 3.3k; r_0402; Mouser Part No. 71-CRCW0402J-3.3K-E3; Digikey Number RHM3.3KBGCT-ND

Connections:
+3V3: D4001.3 (cathode); also elsewhere on the board
/Industrial Input 0/A/D_Input: R4001.1; also elsewhere on the board
/Industrial Input 0/MCU_Input: C4001.1, D4001.2 (AK), R4001.2; also elsewhere on the board
GND: C4001.2, D4001.1 (Anode); also elsewhere on the board

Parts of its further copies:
C5001, C6001, C7001: 1nF; c_0402; Mouser Part No. 810-C1005C0G2A102J5C; Digikey Number 1276-1913-1-ND
D5001, D6001, D7001: 1SS295; sot23; Mouser Part No. 757-1SS295TE85LF; Digikey Number 1SS295(TE85LF)CT-ND
R5001, R6001, R7001: 3.3k; r_0402; Mouser Part No. 71-CRCW0402J-3.3K-E3; Digikey Number RHM3.3KBGCT-ND

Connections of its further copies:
+3V3: D5001.3 (cathode), D6001.3 (cathode), D7001.3 (cathode); also elsewhere on the board
/Industrial Input 1/A/D_Input: R5001.1; also elsewhere on the board
/Industrial Input 1/MCU_Input: C5001.1, D5001.2 (AK), R5001.2; also elsewhere on the board
/Industrial Input 2/A/D_Input: R6001.1; also elsewhere on the board
/Industrial Input 2/MCU_Input: C6001.1, D6001.2 (AK), R6001.2; also elsewhere on the board
/Industrial Input 3/A/D_Input: R7001.1; also elsewhere on the board
/Industrial Input 3/MCU_Input: C7001.1, D7001.2 (AK), R7001.2; also elsewhere on the board
GND: C5001.2, C6001.2, C7001.2, D5001.1 (Anode), D6001.1 (Anode), D7001.1 (Anode); also elsewhere on the board

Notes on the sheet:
48kHz Single Pole Low Pass Filter
0.7mA @ 24V Input, 210mV drop on Schottky array

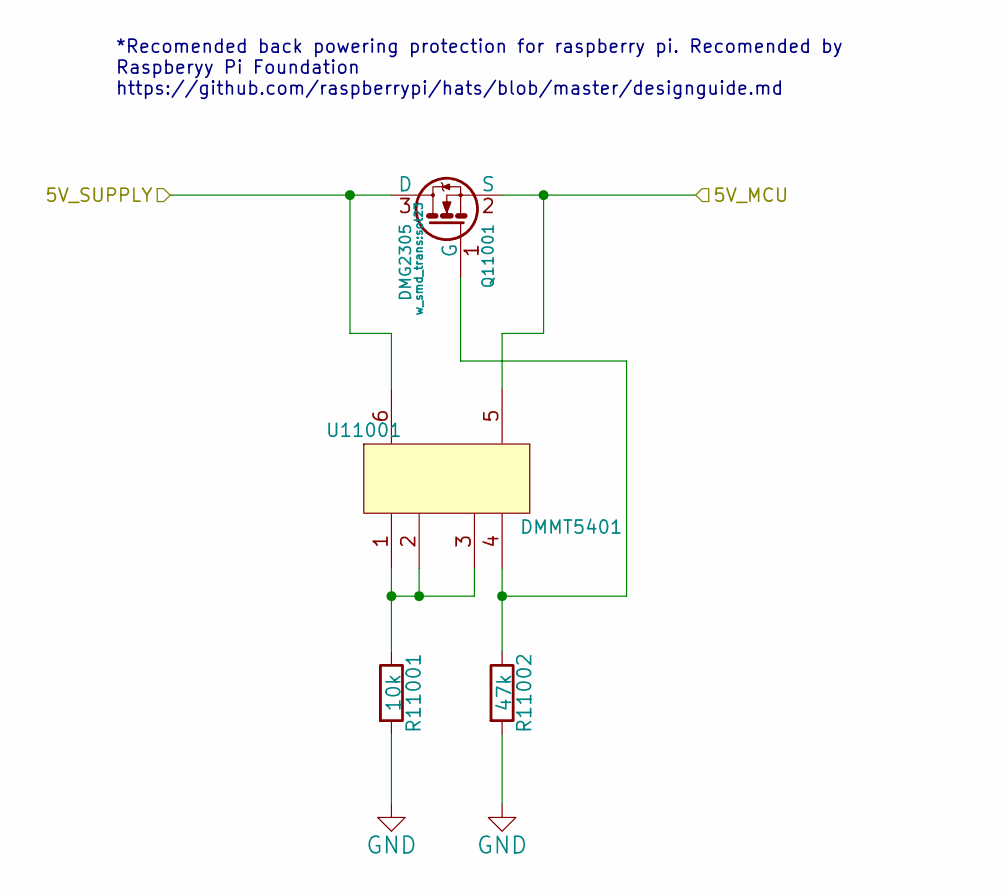
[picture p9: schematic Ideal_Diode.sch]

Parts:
Q11001: DMG2305; sot23; Mouser Part No. 621-DMG2305UX-13
R11001: 10k; r_0402; Mouser Part No. 71-CRCW0402-10K-E3
R11002: 47k; r_0402; Mouser Part No. 667-ERJ-2RKF4702X
U11001: DMMT5401; sot23-6; Mouser Part No. 621-DMMT5401-7-F

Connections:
+5V: Q11001.3 (D), U11001.6; also elsewhere on the board
/Back Power Protection/5V_MCU: Q11001.2 (S), U11001.5; also elsewhere on the board
GND: R11001.2, R11002.2; also elsewhere on the board
unnamed: Q11001.1 (G), R11002.1, U11001.4
unnamed: R11001.1, U11001.1, U11001.2, U11001.3

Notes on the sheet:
*Recomended back powering protection for raspberry pi. Recomended by Raspberyy Pi Foundation https://github.com/raspberrypi/hats/blob/master/designguide.md

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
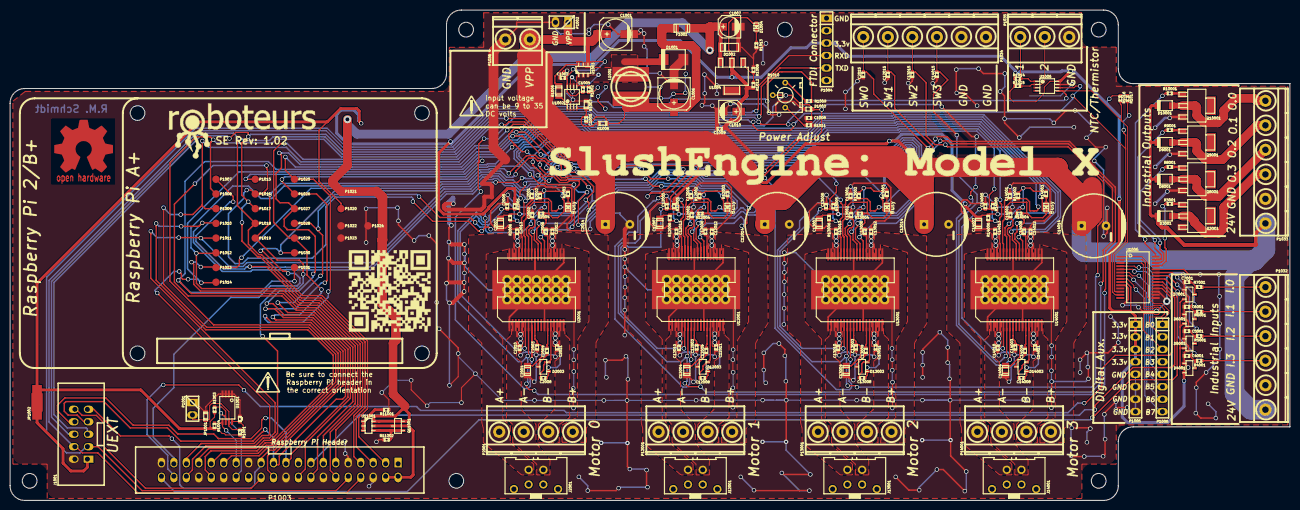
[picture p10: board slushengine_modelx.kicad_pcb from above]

Board: 2 copper layers, 261.0 x 100.0 mm, 216 parts (0 on the bottom side), 117 nets.

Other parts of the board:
MountingHole_3mm, MountingHole_3mm#2, MountingHole_3mm#3, MountingHole_3mm#4, MountingHole_3mm#5, MountingHole_3mm#6, MountingHole_3mm#7, MountingHole_3mm#8, MountingHole_3mm#9, MountingHole_3mm#10: VAL**; MountingHole_3mm

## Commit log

2015-06-15 added some new part numbers
    [Ideal_Diode.sch, Indust_Input.sch, Indust_Output.sch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]
2015-06-15 fixed pour issue by removing chamfers
    [slushengine_modelx.kicad_pcb]
2015-06-15 added board photo
2015-06-15 small board changes
    [slushengine_modelx.kicad_pcb, slushengine_modelx.sch]
2015-06-15 initial commit of contrib file
    [slushengine_modelx.kicad_pcb]
